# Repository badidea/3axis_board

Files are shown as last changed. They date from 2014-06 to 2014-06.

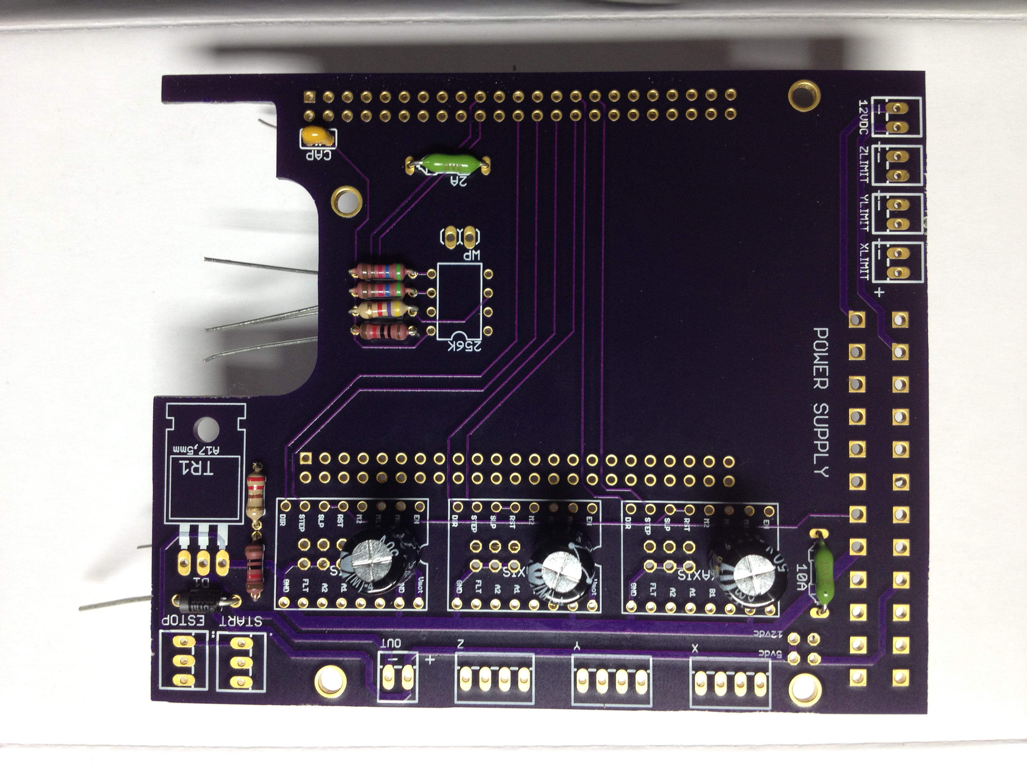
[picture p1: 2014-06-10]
Front.JPG

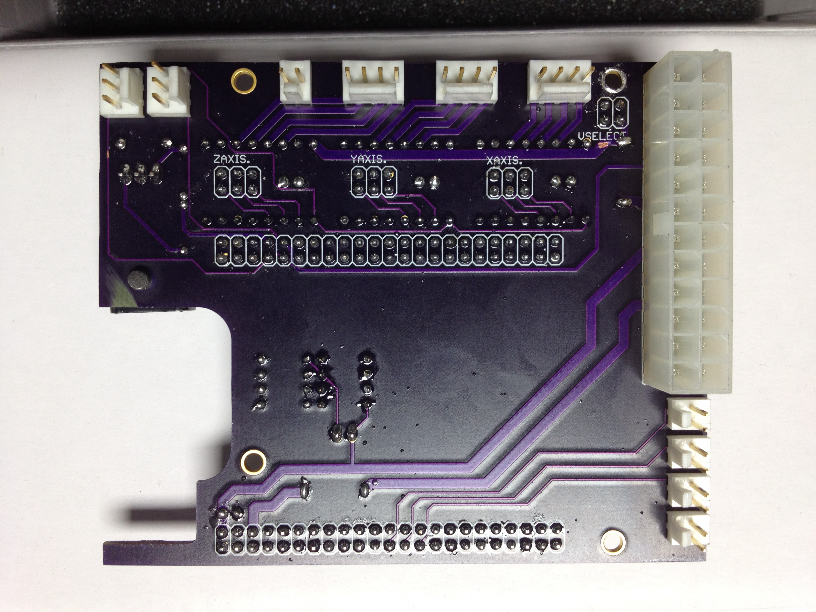
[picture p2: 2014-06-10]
BackDone.JPG

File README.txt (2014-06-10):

3 axis Interface board for Beaglebone Black tenatively called StepOneCNC 

Info:
Designed to support a 3 axis machine with a spindle or engraving head.

Features:
-Designed to play well with Machinekit (that is the hope anyway)
-uses standard ATX power supply with 24 pin connector
-Polulu DRV8825 based stepper drivers (jumpers to set microstep)
-3 digital inputs for homing prox switches (NC sinking)
-1 digital input (cycle start push button)
-1 digital input / stepper driver enable by NC locking push button (estop push button)
-1 transistor output for spindle/laser/relay/solenoid voltage selectable by jumper (5vdc or 12vdc)
-1 12vdc connection for lcd screen or fan

Board was designed in Eagle Lite 6.4.0 and meets OSH Park rule set.

Screen:
7" Capacitive multi-touch screen http://www.chalk-elec.com/?page_id=1280#!/~/product/category=3094861&id=21750201
Mini-HDMI to Micro-HDMI http://www.ebay.com/itm/6FT-1-8m-Mini-HDMI-to-Micro-HDMI-Cable-Cord-Full-HD-1080P-Adapter-Connector-/330909549723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
Mini-USB to USB included with Beaglebone to connect Touch

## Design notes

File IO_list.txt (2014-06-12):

StepOneCNC I/O list

BB_Input (hal_bb_gpio)
P8.7 Estop (107)
P8.9 Cycle Start(109)
P9.23 X Home (223)
P9.25 Y Home (225)
P9.27 Z Home (227)

BB_Output (hal_bb_gpio)
P8.8 Spindle (108)
P8.10 PWS_ON (110)
P8.12 Stepper_EN (112)

Stepper_Outputs  (hal_generic_pru)
P9.31 X_Step (142)
P9.29 X_Dir (143)
P9.30 Y_Step (144)
P9.28 Y_Dir (145)
P9.26 Z_Step (46)
P9.24 Z_Dir (47)

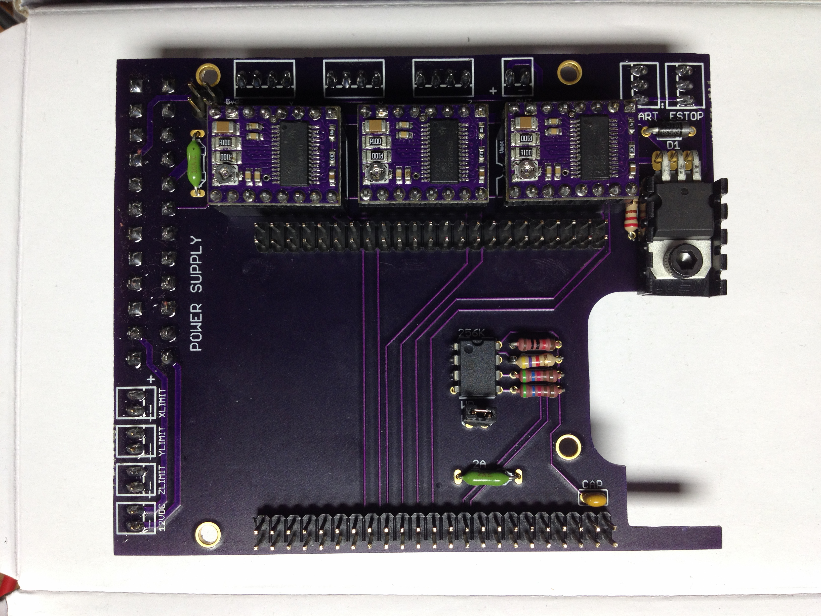
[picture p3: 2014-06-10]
FrontDone.JPG

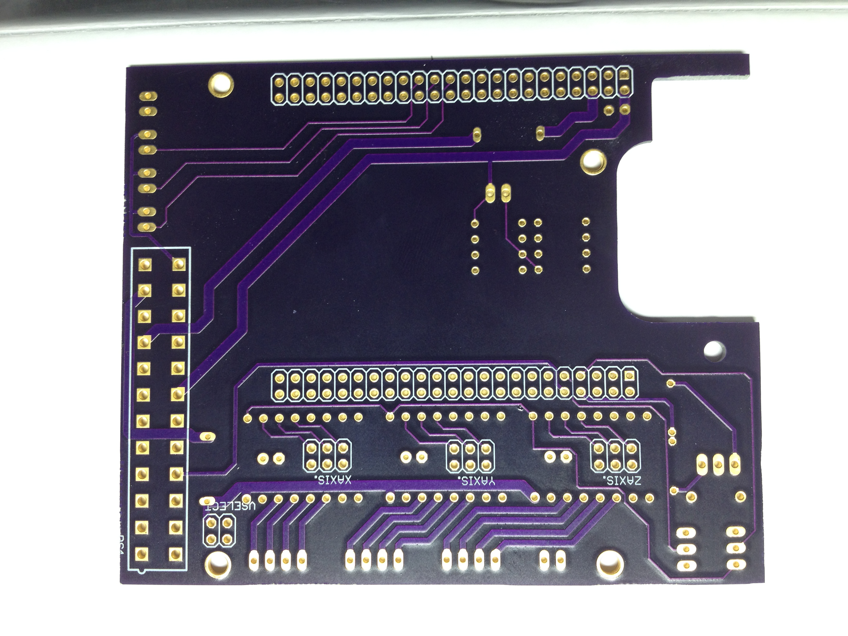
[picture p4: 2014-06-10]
BackEmpty.JPG

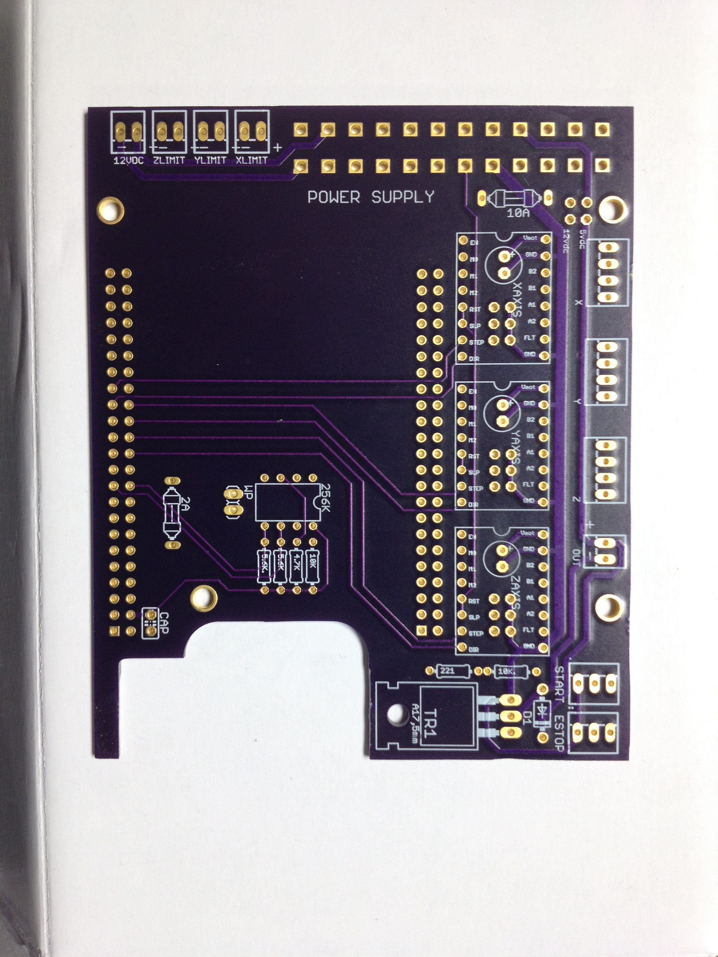
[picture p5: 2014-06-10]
FrontEmpty.JPG

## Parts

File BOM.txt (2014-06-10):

Initial draft of BOM:
-All part numbers were obtained from Newark unless noted.

On board:
(1)  39-28-1243  Molex 24pin ATX connector
(1)  CAT24C256LI-G 256k eeprom
(2)  MCMF0W2FF1002A10 10k ohm resistor
(1)  MCMF0W2FF4701A10 4.7k ohm resistor
(2)  MCMF0W2FF5602A10 5.6k ohm resistor
(1)  MCMF0W2FF2200A10 220 ohm resistor
(1)  MC0805B104K500A2.54MM .1uF 50v capacitor
(3)  22-11-2042 Molex 4 pin connector
(5)  22-11-2022 Molex 2 pin connector
(2)  22-11-2032 Molex 3 pin connector
(2)  M20-9983645  72 way 2 row pin header
(6)  2212S-08SG-85 8 way 1 row pin socket 
(3)  URZ1H101MPD1TD 100uF 50v capacitor
(1)  0251010.MRT1L 10a pico fuse
(1)  0251002.MAT1L 2a pico fuse
(1)  STP40NF10L Mosfet
(1)  1N5953BG zener diode

Not on board but required:
(5)  22-01-3027  Molex 2 pin female connector
(3)  22-01-3047  Molex 4 pin female connector
(2)  22-01-3037  Molex 3 pin female connector
(30+)  08-50-0113  Molex pins crimp style
(6)  2211S-08G  8 way 1 row pin header 
(1)  SPC19807 pack of 25 jumpers

Either Element14 version or CircuitCo version should work
(1)  BBONE-BLACK-4G REVC Beaglebone black

From Pololu.com
(3)  Pololu (http://www.pololu.com/product/2133) DRV8825 stepper drivers w/carrier

Chalk-Elec 7" HDMI Capacitive MultiTouch screen
Passive 4 Port USB Hub
Keyboard
ATX Power Supply
WIFI Adapter Logic Supply UWN-100

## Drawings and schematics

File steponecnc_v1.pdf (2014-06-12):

+ -

| 12vdc

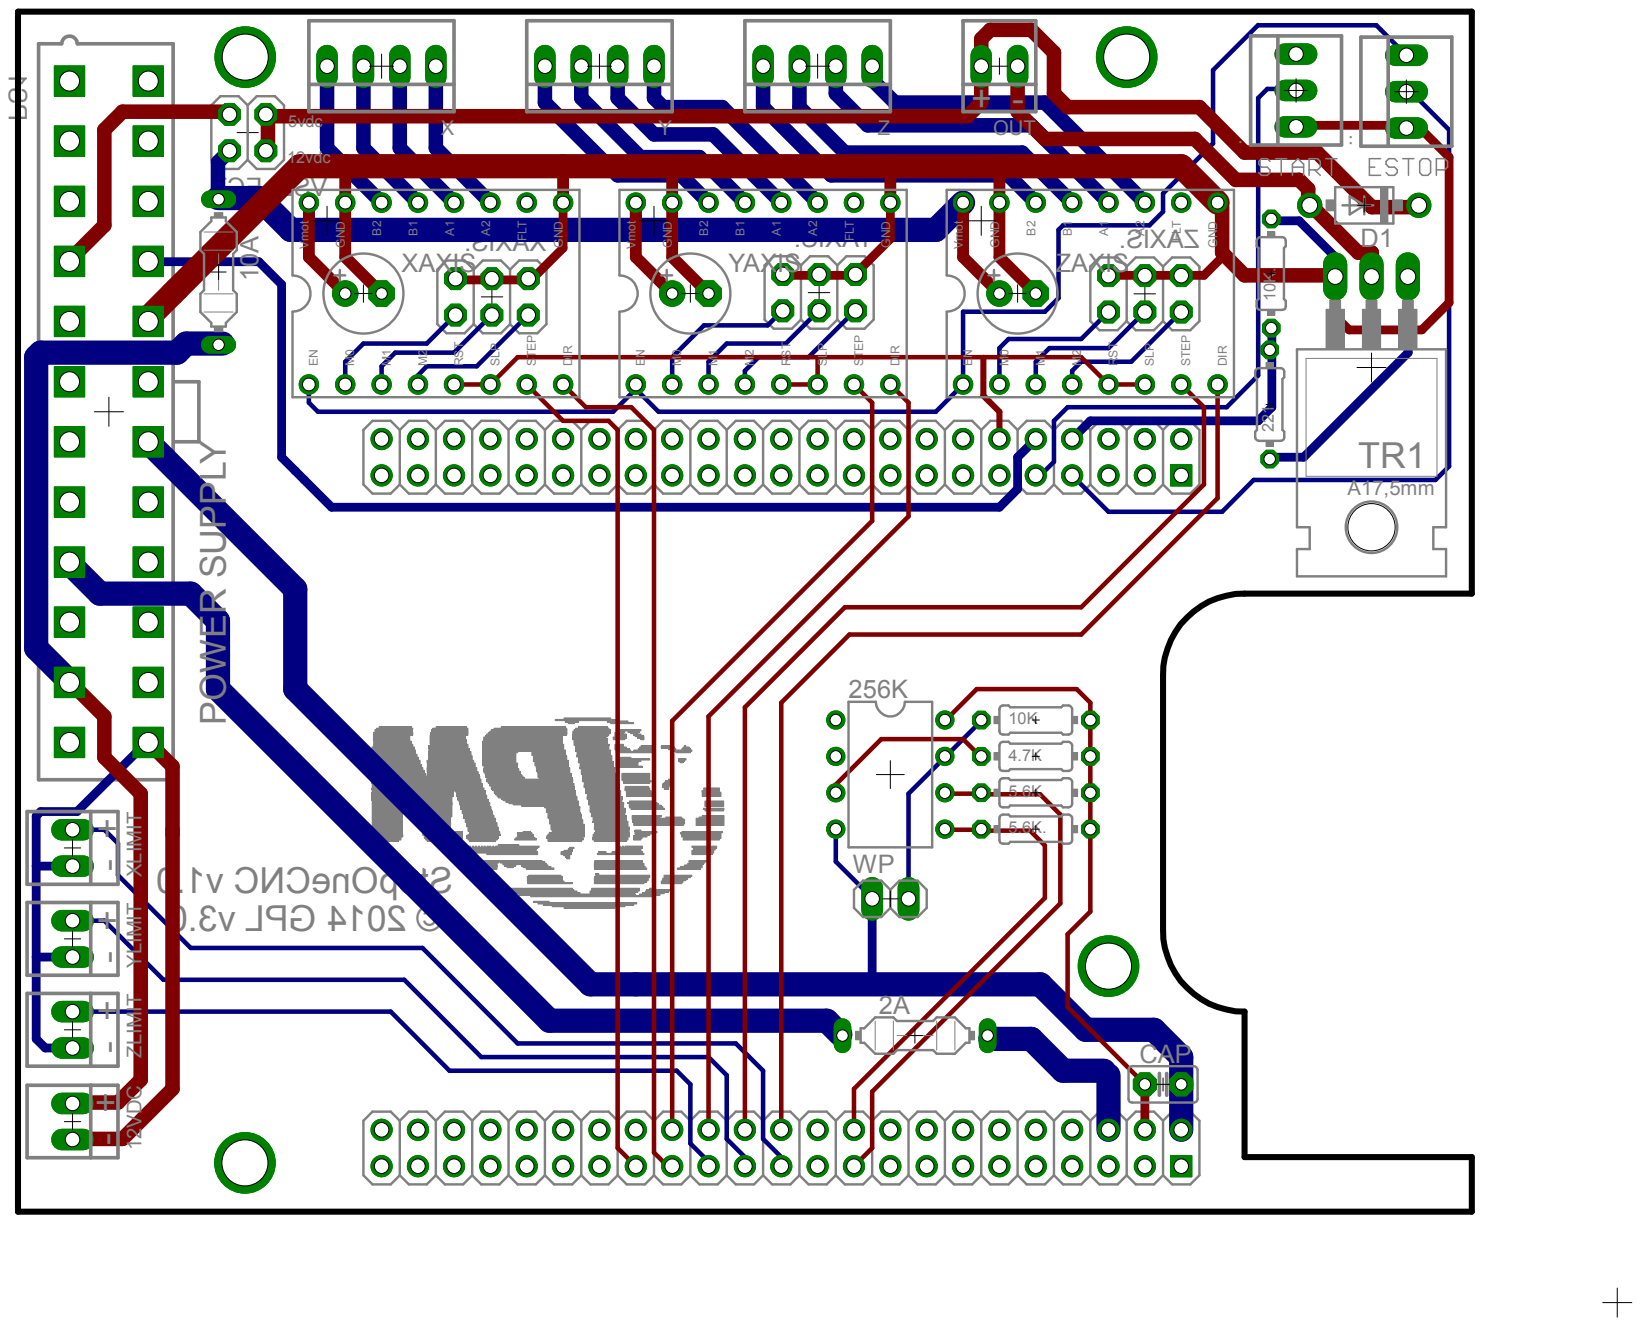
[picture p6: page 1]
RST; STEP; DIR; Vmot; GND; FLT; SLP; POWER SUPPLY; 5vdc; CAP; XAXIS; YAXIS; ZAXIS; OUT; 12VDC

XLIMIT YLIMIT ZLIMIT

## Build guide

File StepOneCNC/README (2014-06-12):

This configuration drives a standard 3-axis Milling/Laser/Engraving machine using the PRU for
high speed step/dir pulse generation and a StepOneCNC driver board.  The
StepOneCNC configuration is for the a BBB rev.C using the eMMC and HDMI.

There are currently no limit switches configured, so adjust the MIN_LIMIT
and MAX_LIMIT axis settings in the ini file if your printer has less than
? inches of X/ ? inches of Y travel.

Adjust as required for your machine.  Make scale negative to invert any
axis that is moving 'backwards'.

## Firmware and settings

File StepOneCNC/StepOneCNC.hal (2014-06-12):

# #######################################
#
# HAL file for StepOneCNC Cape with 3 steppers
#
# Derived from example hm2-stepper config
#
# ########################################

# Launch the setup script to make sure hardware setup looks good
loadusr -w ./setup.sh


# ###################################
# Core EMC/HAL Loads
# ###################################

# kinematics
loadrt trivkins

# motion controller, get name and thread periods from ini file
loadrt [EMCMOT]EMCMOT servo_period_nsec=[EMCMOT]SERVO_PERIOD num_joints=[TRAJ]AXES


# load low-level drivers
loadrt hal_bb_gpio output_pins=108,110,112 input_pins=107,109,223,225,227
loadrt [PRUCONF](DRIVER) prucode=$(LINUXCNC_HOME)/[PRUCONF](PRUBIN) [PRUCONF](CONFIG)
loadrt limit1 count=1


# ################################################
# THREADS
# ################################################

addf [PRUCONF](DRIVER).capture-position   servo-thread
addf bb_gpio.read                         servo-thread
addf motion-command-handler               servo-thread
addf motion-controller                    servo-thread
addf limit1.0                             servo-thread
addf [PRUCONF](DRIVER).update             servo-thread
addf bb_gpio.write                        servo-thread


# ######################################################
# Axis-of-motion Specific Configs (not the GUI)
# ######################################################


# ################
# X [0] Axis
# ################

# axis enable chain
newsig emcmot.00.enable bit
sets emcmot.00.enable FALSE
net emcmot.00.enable <= axis.0.amp-enable-out 
net emcmot.00.enable => [PRUCONF](DRIVER).stepgen.00.enable


# position command and feedback
net emcmot.00.pos-cmd <= axis.0.motor-pos-cmd
net emcmot.00.pos-cmd => [PRUCONF](DRIVER).stepgen.00.position-cmd

net motor.00.pos-fb <= [PRUCONF](DRIVER).stepgen.00.position-fb
net motor.00.pos-fb => axis.0.motor-pos-fb


# timing parameters
setp [PRUCONF](DRIVER).stepgen.00.dirsetup        [AXIS_0]DIRSETUP
setp [PRUCONF](DRIVER).stepgen.00.dirhold         [AXIS_0]DIRHOLD

setp [PRUCONF](DRIVER).stepgen.00.steplen         [AXIS_0]STEPLEN
setp [PRUCONF](DRIVER).stepgen.00.stepspace       [AXIS_0]STEPSPACE

setp [PRUCONF](DRIVER).stepgen.00.position-scale  [AXIS_0]SCALE

setp [PRUCONF](DRIVER).stepgen.00.maxvel          [AXIS_0]STEPGEN_MAX_VEL
setp [PRUCONF](DRIVER).stepgen.00.maxaccel        [AXIS_0]STEPGEN_MAX_ACC

#setp [PRUCONF](DRIVER).stepgen.00.step_type       0
# P9.31 PRU1.out2
setp [PRUCONF](DRIVER).stepgen.00.steppin         142
# P9.29 PRU1.out4
setp [PRUCONF](DRIVER).stepgen.00.dirpin          143


# ################
# Y [1] Axis
# ################

# axis enable chain
newsig emcmot.01.enable bit
sets emcmot.01.enable FALSE

net emcmot.01.enable <= axis.1.amp-enable-out 
net emcmot.01.enable => [PRUCONF](DRIVER).stepgen.01.enable


# position command and feedback
net emcmot.01.pos-cmd <= axis.1.motor-pos-cmd
net emcmot.01.pos-cmd => [PRUCONF](DRIVER).stepgen.01.position-cmd

net motor.01.pos-fb <= [PRUCONF](DRIVER).stepgen.01.position-fb
net motor.01.pos-fb => axis.1.motor-pos-fb


# timing parameters
setp [PRUCONF](DRIVER).stepgen.01.dirsetup        [AXIS_1]DIRSETUP
setp [PRUCONF](DRIVER).stepgen.01.dirhold         [AXIS_1]DIRHOLD

setp [PRUCONF](DRIVER).stepgen.01.steplen         [AXIS_1]STEPLEN
setp [PRUCONF](DRIVER).stepgen.01.stepspace       [AXIS_1]STEPSPACE

setp [PRUCONF](DRIVER).stepgen.01.position-scale  [AXIS_1]SCALE

setp [PRUCONF](DRIVER).stepgen.01.maxvel          [AXIS_1]STEPGEN_MAX_VEL
setp [PRUCONF](DRIVER).stepgen.01.maxaccel        [AXIS_1]STEPGEN_MAX_ACC

#setp [PRUCONF](DRIVER).stepgen.01.step_type       0
# P9.30 PRU1.out5
setp [PRUCONF](DRIVER).stepgen.01.steppin         144
# P9.28 PRU1.out6
setp [PRUCONF](DRIVER).stepgen.01.dirpin          145


# ################
# Z [2] Axis
# ################

# axis enable chain
newsig emcmot.02.enable bit
sets emcmot.02.enable FALSE

net emcmot.02.enable <= axis.2.amp-enable-out 
net emcmot.02.enable => [PRUCONF](DRIVER).stepgen.02.enable


# position command and feedback
net emcmot.02.pos-cmd <= axis.2.motor-pos-cmd
net emcmot.02.pos-cmd => [PRUCONF](DRIVER).stepgen.02.position-cmd

net motor.02.pos-fb <= [PRUCONF](DRIVER).stepgen.02.position-fb
net motor.02.pos-fb => axis.2.motor-pos-fb


# timing parameters
setp [PRUCONF](DRIVER).stepgen.02.dirsetup        [AXIS_2]DIRSETUP
setp [PRUCONF](DRIVER).stepgen.02.dirhold         [AXIS_2]DIRHOLD

setp [PRUCONF](DRIVER).stepgen.02.steplen         [AXIS_2]STEPLEN
setp [PRUCONF](DRIVER).stepgen.02.stepspace       [AXIS_2]STEPSPACE

setp [PRUCONF](DRIVER).stepgen.02.position-scale  [AXIS_2]SCALE

setp [PRUCONF](DRIVER).stepgen.02.maxvel          [AXIS_2]STEPGEN_MAX_VEL
setp [PRUCONF](DRIVER).stepgen.02.maxaccel        [AXIS_2]STEPGEN_MAX_ACC

#setp [PRUCONF](DRIVER).stepgen.02.step_type       0
# P9.26 PRU1.out8
setp [PRUCONF](DRIVER).stepgen.02.steppin         46
# P9.24 PRU1.out9
setp [PRUCONF](DRIVER).stepgen.02.dirpin          47



# ##################################################
# Standard I/O - EStop, Enables, Limit Switches, Etc
# ##################################################

# Estop Signal 
net estop_loop bb_gpio.p8.in-07 => iocontrol.0.emc-enable-in
setp bb_gpio.p8.in-07.invert 1

# Stepper Enable
net emcmot.00.enable => bb_gpio.p8.out-12

# create signals for tool loading loopback
net tool-prep-loop iocontrol.0.tool-prepare => iocontrol.0.tool-prepared
net tool-change-loop iocontrol.0.tool-change => iocontrol.0.tool-changed

# Machine power
# Use halui.machine.is-on instead?
net emcmot.00.enable => bb_gpio.p8.out-10
setp bb_gpio.p8.out-10.invert 1

#Cycle Start Button
#Should start the currently loaded program (for repeating parts)
net halui.program.run <= bb_gpio.p8.in-09
#setp bb_gpio.p8.in-09.invert 1

#Spindle Start
net spindle-fwd motion.spindle-forward => bb_gpio.p8.out-08



# ################
# Limit Switches
# ################
net limit-x-min <= bb_gpio.p9.in-23
net limit-y-min <= bb_gpio.p9.in-25
net limit-z-min <= bb_gpio.p9.in-27

# Adjust as needed for your switch polarity
setp bb_gpio.p9.in-23.invert 1
setp bb_gpio.p9.in-25.invert 1
setp bb_gpio.p9.in-27.invert 1

# Uncomment if you actually have limit switches setup
# You probably want to setup homing in the INI file, as well
net limit-x-min => axis.0.home-sw-in
net limit-y-min => axis.1.home-sw-in
net limit-z-min => axis.2.home-sw-in

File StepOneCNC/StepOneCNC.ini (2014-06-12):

[PRUCONF]
DRIVER=hal_pru_generic
CONFIG=pru=1 num_stepgens=3 num_pwmgens=0
PRUBIN=rtlib/xenomai/pru_generic.bin


[EMC]

# Name of machine, for use with display, etc.
MACHINE =               StepOneCNC

# Debug level, 0 means no messages. See src/emc/nml_int/emcglb.h for others
#DEBUG =                0x00000003
#DEBUG =                0x00000007
DEBUG = 0




[DISPLAY]

# Name of display program, e.g., tkemc
DISPLAY = tkemc
#DISPLAY = gscreen
#DISPLAY = axis

# Touchy currently won't work without some hardware buttons/jog-wheel
#DISPLAY = touchy

# Cycle time, in seconds, that display will sleep between polls
CYCLE_TIME =            0.200

# Path to help file
HELP_FILE =             tklinucnc.txt

# Initial display setting for position, RELATIVE or MACHINE
POSITION_OFFSET =       RELATIVE

# Initial display setting for position, COMMANDED or ACTUAL
POSITION_FEEDBACK =     ACTUAL

# Highest value that will be allowed for feed override, 1.0 = 100%
MAX_FEED_OVERRIDE =     1.5

# Prefix to be used
PROGRAM_PREFIX = /home/machinekit/linuxcnc/nc_files

# Introductory graphic
INTRO_GRAPHIC =         linuxcnc.gif
INTRO_TIME =            5

# Increments for the JOG section
INCREMENTS = 10 1 0.1 0.01


#PYVCP = 3D.Temps.panel.xml

[FILTER]
PROGRAM_EXTENSION = .png,.gif,.jpg Grayscale Depth Image
PROGRAM_EXTENSION = .py Python Script
png = image-to-gcode
gif = image-to-gcode
jpg = image-to-gcode
py = python


[TASK]

# Name of task controller program, e.g., milltask
TASK =                  milltask

# Cycle time, in seconds, that task controller will sleep between polls
CYCLE_TIME =            0.010




[RS274NGC]

# File containing interpreter variables
PARAMETER_FILE =        pru-stepper.var




[EMCMOT]

EMCMOT =                motmod

# Timeout for comm to emcmot, in seconds
COMM_TIMEOUT =          1.0

# Interval between tries to emcmot, in seconds
COMM_WAIT =             0.010

# Servo task period, in nanoseconds
SERVO_PERIOD =          1000000




[HAL]

# The run script first uses halcmd to execute any HALFILE
# files, and then to execute any individual HALCMD commands.

# list of hal config files to run through halcmd
# files are executed in the order in which they appear

HALFILE =		StepOneCNC.hal

# list of halcmd commands to execute
# commands are executed in the order in which they appear
#HALCMD =               save neta

POSTGUI_HALFILE =       StepOneCNC.postgui.hal


[TRAJ]

AXES =                  3
COORDINATES =           X Y Z
MAX_ANGULAR_VELOCITY = 1.00
DEFAULT_ANGULAR_VELOCITY = .50
LINEAR_UNITS =          inch
ANGULAR_UNITS =         degree
CYCLE_TIME =            0.010
DEFAULT_VELOCITY = 1.0
MAX_LINEAR_VELOCITY = 1.5





[AXIS_0]

# 
# Step timing is 40 us steplen + 40 us stepspace
# That gives 80 us step period = 12.5 KHz step freq
#
# Bah, even software stepping can handle that, hm2 doesnt buy you much with
# such slow steppers.
#
# Scale is 200 steps/rev * 5 revs/inch = 1000 steps/inch
#
# This gives a maxvel of 12.5/1 = 12.5 ips
#


TYPE =              LINEAR
MAX_VELOCITY =       2.0
MAX_ACCELERATION =   40.0
# Set Stepgen max 20% higher than the axis
STEPGEN_MAX_VEL =    2.4
STEPGEN_MAX_ACC =    48.0

BACKLASH =           0.000

# scale is 200 steps/rev * 5 revs/inch
SCALE =  2000

MIN_LIMIT =             -1.0
MAX_LIMIT =             220.0

FERROR =     1.0
MIN_FERROR = 0.1

HOME =                  0.000
HOME_OFFSET =           0.00
HOME_IGNORE_LIMITS =    YES
HOME_USE_INDEX =        NO
HOME_SEQUENCE =         0

# Set to zero if you don't have physical home/limit switches
# Set to the desired homing and latch velocity if you have switches
# See: http://www.linuxcnc.org/docs/2.5/html/config/ini_homing.html
HOME_SEARCH_VEL =       0.0
HOME_LATCH_VEL =        0.0

# these are in nanoseconds
DIRSETUP   =              200
DIRHOLD    =              200
STEPLEN    =              2000
STEPSPACE  =              2000




[AXIS_1]

TYPE =              LINEAR
MAX_VELOCITY =       2.0
MAX_ACCELERATION =   40.0
# Set Stepgen max 20% higher than the axis
STEPGEN_MAX_VEL =    2.4
STEPGEN_MAX_ACC =    48.0

BACKLASH =           0.000

SCALE =  2000

MIN_LIMIT =             -1.0
MAX_LIMIT =             250.0

FERROR =     1.0
MIN_FERROR = 0.1

HOME =                  0.000
HOME_OFFSET =           0.00
HOME_IGNORE_LIMITS =    YES
HOME_USE_INDEX =        NO
HOME_SEQUENCE =         0

# Set to zero if you don't have physical home/limit switches
# Set to the desired homing and latch velocity if you have switches
# See: http://www.linuxcnc.org/docs/2.5/html/config/ini_homing.html
HOME_SEARCH_VEL =       0.0
HOME_LATCH_VEL =        0.0

# these are in nanoseconds
DIRSETUP   =              200
DIRHOLD    =              200
STEPLEN    =              2000
STEPSPACE  =              2000




[AXIS_2]

TYPE =              LINEAR
MAX_VELOCITY =      5.0
MAX_ACCELERATION =  40.00
# Set Stepgen max 20% higher than the axis
STEPGEN_MAX_VEL =    6.0
STEPGEN_MAX_ACC =    48.0

BACKLASH =           0.000

SCALE = 2000

MIN_LIMIT =             -10.0
MAX_LIMIT =             200.0

FERROR =     1.0
MIN_FERROR = 0.1

HOME =                  0.000
HOME_OFFSET =           0.00
HOME_IGNORE_LIMITS =    YES
HOME_USE_INDEX =        NO
HOME_SEQUENCE =         0

# Set to zero if you don't have physical home/limit switches
# Set to the desired homing and latch velocity if you have switches
# See: http://www.linuxcnc.org/docs/2.5/html/config/ini_homing.html
HOME_SEARCH_VEL =       0.0
HOME_LATCH_VEL =        0.0

# these are in nanoseconds
DIRSETUP   =              200
DIRHOLD    =              200
STEPLEN    =              2000
STEPSPACE  =              2000




[EMCIO]

# Name of IO controller program, e.g., io
EMCIO =                 io

# cycle time, in seconds
CYCLE_TIME =            0.100

# tool table file
TOOL_TABLE =            tool.tbl

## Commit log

2014-04-29 initial board file
    [stepone_v1.brd]
2014-05-02 updates to bom/eagle file
    [steponecnc_v1.brd]
2014-05-02 board change
    flipped atx connector and changed #PSON to be fired from beaglebone gpio
2014-06-10 updated after initial build
    still a work in progress but first version is built
    [steponecnc_v1.brd]
2014-06-10 added pdf of board
2014-06-12 Added Linuxcnc config
    [StepOneCNC.hal, StepOneCNC.postgui.hal, steponecnc_v1.brd]
2014-06-20 changed how microstep jumpers are connected
    [steponecnc_v1.brd]
